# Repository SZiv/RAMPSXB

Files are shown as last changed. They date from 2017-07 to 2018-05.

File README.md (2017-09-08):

# RAMPSXB
For anyone who does extensive, hardcore, overkill 3D printer work, will typically run out of either stepper motor slots for extruders, MOSFETS for Heaters/fans, or Thermistor pins. The options for this are to either upgrade to an expensive mainboard like a duet, or add on individial drivers for stepper or FET. There isn't really a cheap or easy option. 

Now there is! RAMPSXB is an expansion board for the popular control board RAMPS 1.4 that connects to the AUX and endstop headers like an arduino shield to add functionality to the system. in addition, most components and schematic layouts follow the Reprap Defacto standard, as well as the original RAMPS board, so the thermistors, FETs, microstepping and drivers should all behave as if they were an extension of the RAMPS board itself. Most components are dirt cheap, and the board can be outsourced and assembled with a simple soldering iron. 

RAMPSXB is an expansion board shield for serious 3D printer people that adds an overkill amount of functionality to run high-end extruder systems like the E3D Kraken or Diamond Full Color Hotend: 

- 4 additional Stepper motors (bringing the total to 9; enough to run 6 extruders) 
- 4 additional Thermistor pins
- 4 additional MOSFETs w/ PWM control
- EXP1 and EXP2 headers for a Reprap Full Graphics Smart Controller (With SD Card)
- 4 additional 12V rail pins w/ grounds
- 4 additional 5V rail pins w/ grounds
- 2 steppers have two rows of output pins for driving 2 motors together
- Broken out, preregulated pins for HC-05 Bluetooth Chip
- Isolated input and microcontroller power, so 12V or 24V power can be used for the FETs. 
- Suppression Capacitors on endstops to reduce false positives caused by inductive voltages.
- 1 servo pin (the other 3 were consumed for PWM on the FETs, but are broken out if you want to use them for something other than the FETS)
- Broken out 12C pins 

This comes at the cost of: 
- 3 of the 4 servo pins. 
- Max endstops (there are only min endstops)
- AAAAAAALL the AUX headers (with the exception of 1 digital pin, D40, which is broken out)
- A lot of additional space

If you have questions, feel free to shoot me a message, or if you want to learn more about the making of this project, see here: http://scottziv.com/rampsxb

Be sure to take a look at the Wiki here: http://reprap.org/wiki/RAMPSXB

Happy printing!

Released under GPL V3

# Pin Definitions

E2 Direction      -  15  
E2 Step           -  19  
E2 Enable         -  63  
E3 Direction      -  2  
E3 Step           -  39  
E3 Enable         -  58  
E4 Direction      -  42  
E4 Step           -  44  
E4 Enable         -  43  
E5 Direction      -  32  
E5 Step           -  47  
E5 Enable         -  57  
Thermistor T3     -  A11  
Thermistor T4     -  A12  
Thermistor T5     -  A10  
Thermistor T6     -  A5  
MOSFET H3          -  4  
MOSFET H4          -  5  
MOSFET H5          -  6  
MOSFET H6          -  45    

HC-05 chip, LCD screen, and SD card follow the standard pinouts for the Full Graphic smart controller and RAMPS HC-05 attachment.

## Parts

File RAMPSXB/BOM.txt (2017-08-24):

---- Bill of Materials ----  

Part                                      Quantity          Package  

Electrolytic Capacitors, 100uF, SMD         4                 0605  
Electrolytic Capacitors, 10uF, SMD          4                 0405  
Nonpolarized Capacitor, SMD, 0.47uF         3                 0805  
Resistors, SMD, 100k Ohm                    8                 0805  
Resistors, SMD, 10k Ohm                     4                 0805  
Resistors, SMD, 10 Ohm                      4                 0805  
Resistors, SMD, 1.8k Ohm                    4                 0805  
Resistors, SMD, 4.7k Ohm                    4                 0805  
Resistors, SMD, 3.3k Ohm                    1                 0805  
Resistors, SMD, 2.2k Ohm                    1                 0805  
MOSFET, Through-hole, stp55nf06l            4                 TO-220  
LEDs, SMD                                   4                 0805  
Screw Terminals                             5                 3.5mm  
PTC Fuse, 30V 6A-9A                         1                
Pin Headers, 1x18, female, 0.1" spacing     1                 N/A   
Pin Headers, 1x8, female, 0.1" spacing      8                 N/A  
Pin Headers, 2x10, female, 0.1" spacing     1                 N/A  
Pin Headers, 2x4, female, 0.1" spacing      3                 N/A
Pin Headers, 1x4, female, 0.1" spacing      2                 N/A
Pin Headers, 1x6, female, 0.1" spacing      3                 N/A  
Pin Headers, 1x1, male, 0.1" spacing        1                 N/A  
Pin Headers, 2x4, male, 0.1" spacing        6                 N/A  
Pin Headers, 1x4, male, 0.1" spacing        3                 N/A  
Pin Headers, 2x5, male, 0.1" spacing        2                 N/A
Pin Headers, 2x2, male, 0.1" spacing        1                 N/A  
Pin Headers, 1x3, male, 0.1" spacing        4                 N/A

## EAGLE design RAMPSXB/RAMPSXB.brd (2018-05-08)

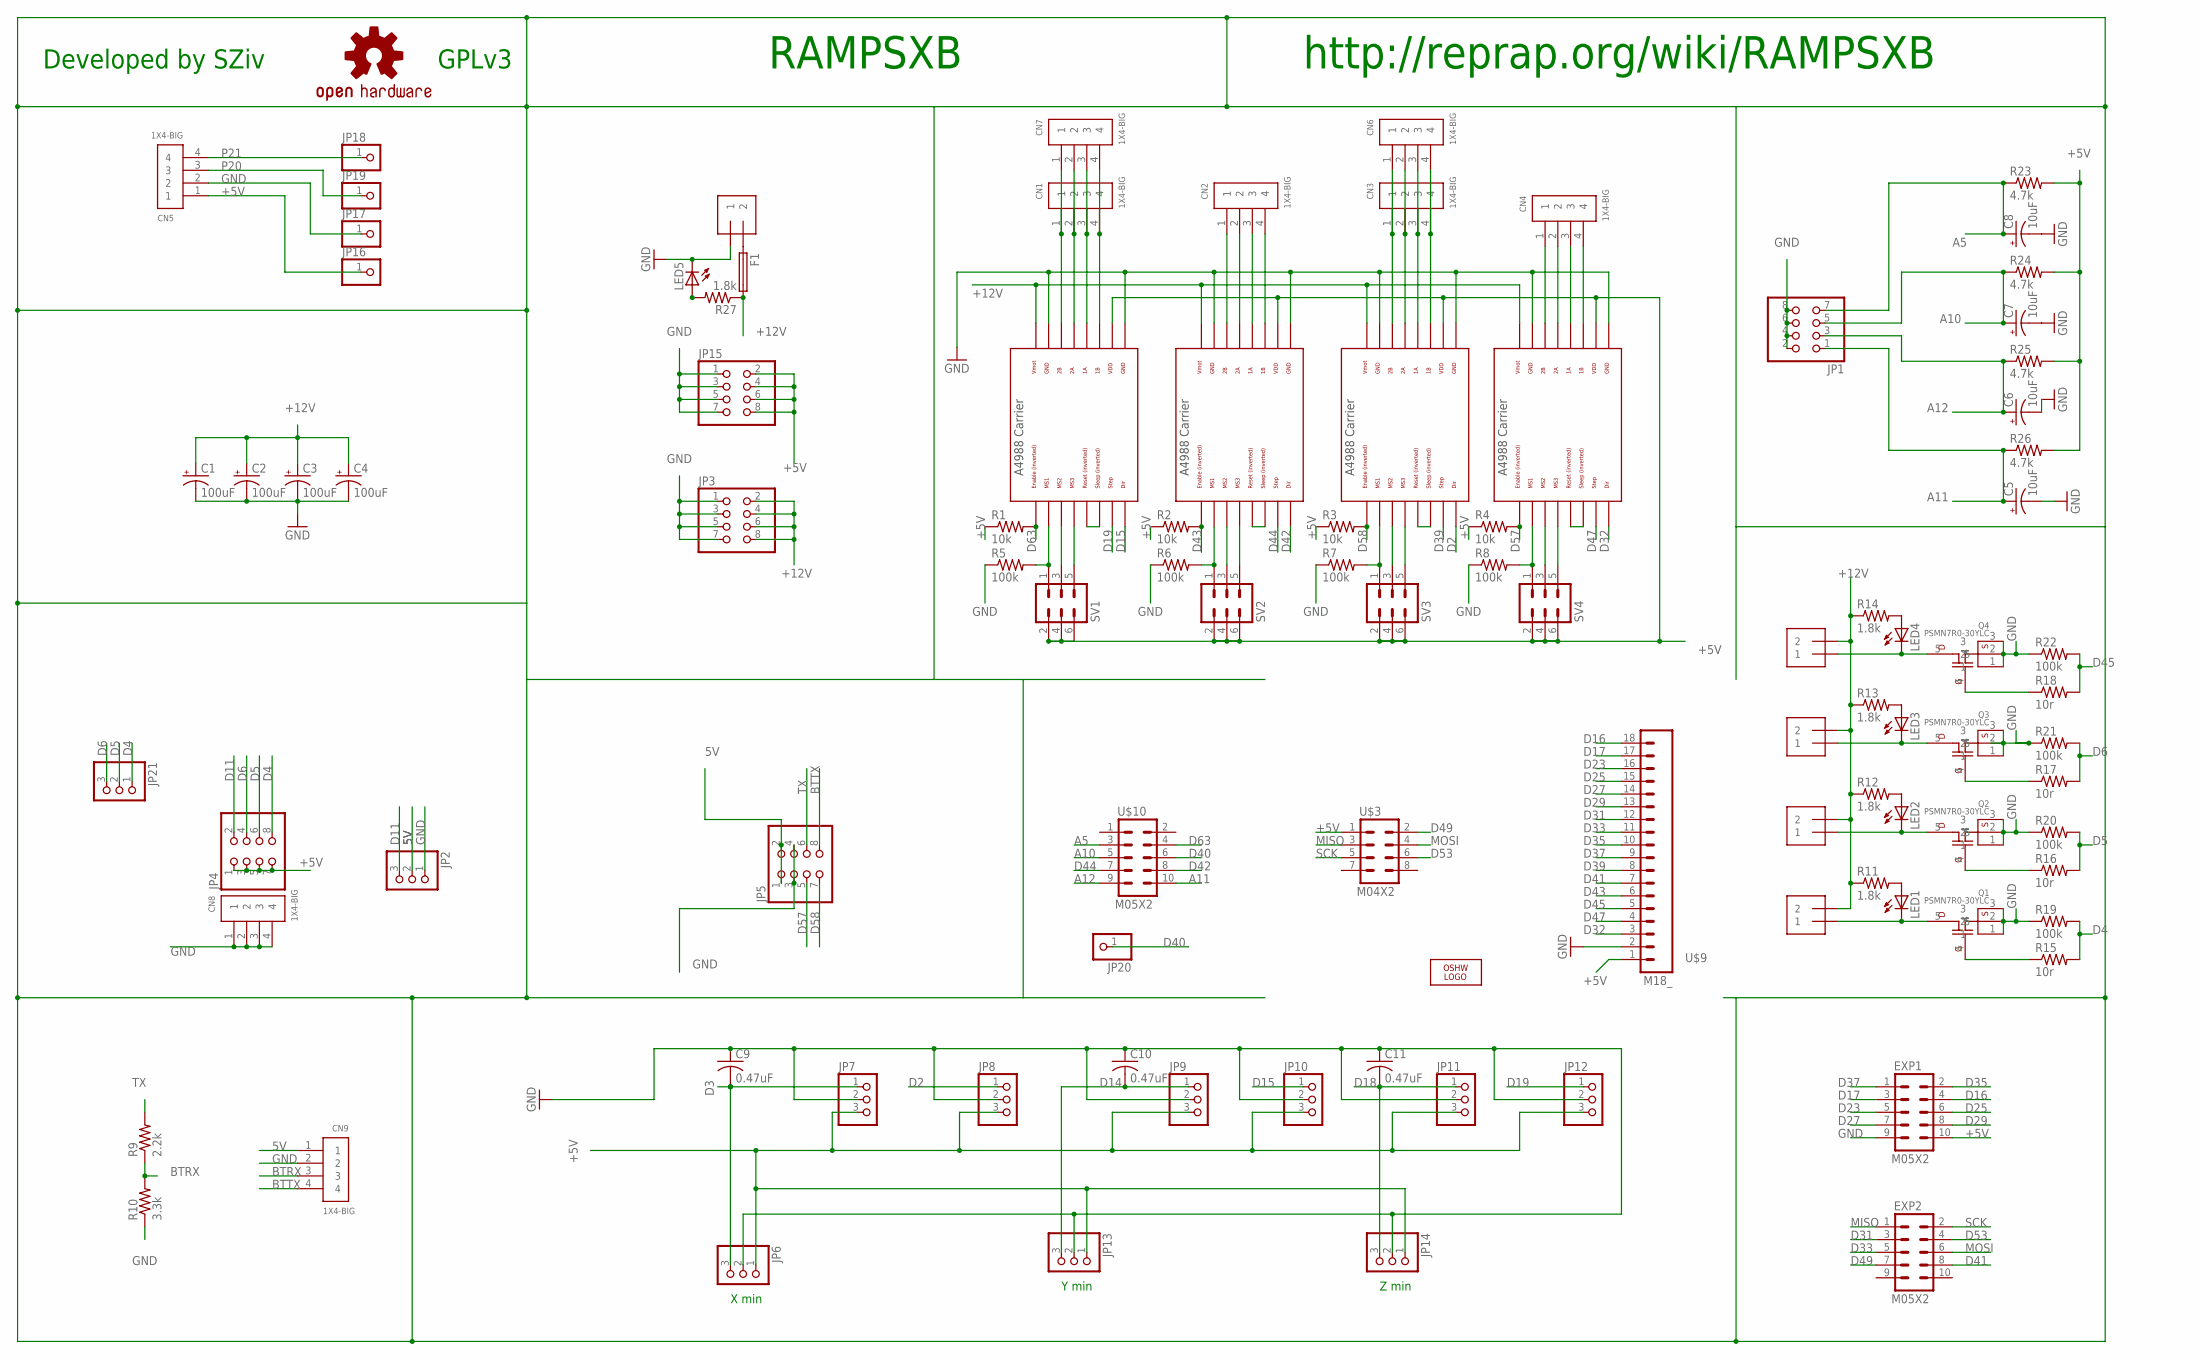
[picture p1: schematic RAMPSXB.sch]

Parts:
C1, C2, C3, C4: 100uF; 153CLV-0605
C5, C6, C7, C8: 10uF; 153CLV-0405
C9, C10, C11: 0.47uF; C0805
CN1, CN2, CN3, CN4, CN5, CN6, CN7, CN8, CN9: 1X4-BIG; 1X04-BIG
EXP1, EXP2: M05X2; 2X5
F1: PTCFUSE; LITTLEFUSE
J1, J2, J3, J4, J5: 1X2-3.5MM
JP1, JP3, JP4, JP5, JP15: PINHD-2X4; 2X04
JP2, JP6, JP7, JP8, JP9, JP10, JP11, JP12, JP13, JP14, JP21: PINHD-1X3; 1X03
JP16, JP17, JP18, JP19, JP20: PINHD-1X1; 1X01
LED1, LED2, LED3, LED4, LED5: LEDCHIPLED_0805; CHIPLED_0805
LOGO1: OSHW_LOGO_6MILX0100-NT; OSHW_6X100_NOTEXT
LOGO2: OSHW-LOGOL; OSHW-LOGO-L
Q1, Q2, Q3, Q4: PSMN7R0-30YLC; LFPAK
R1, R2, R3, R4: 10k; M0805
R5, R6, R7, R8, R19, R20, R21, R22: 100k; M0805
R9: 2.2k; M0805
R10: 3.3k; M0805
R11, R12, R13, R14, R27: 1.8k; M0805
R15, R16, R17, R18: 10r; M0805
R23, R24, R25, R26: 4.7k; R0805
SV1, SV2, SV3, SV4: MA03-2
U$1, U$2, U$4, U$5: POLOLU_A4983CARRIER; A4988BREAKOUT
U$3: M04X2; 2X4
U$9: M18_; 1X18
U$10: M05X2; 2X5

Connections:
5V: CN9.1, JP2.2, JP5.1, JP5.2
+5V: CN5.1, EXP1.10, JP4.1, JP4.3, JP4.5, JP4.7, JP6.1, JP7.3, JP8.3, JP9.3, JP10.3, JP11.3, JP12.3, JP13.1, JP14.1, JP15.2, JP15.4, JP15.6, JP15.8, JP16.1, R1.1, R2.1, R3.1, R4.1, R23.2, R24.2, R25.2, R26.2, SV1.2, SV1.4, SV1.6, SV2.2, SV2.4, SV2.6, SV3.2, SV3.4, SV3.6, SV4.2, SV4.4, SV4.6, U$1.VDD, U$2.VDD, U$3.1, U$4.VDD, U$5.VDD, U$9.1
+12V: C1.+, C2.+, C3.+, C4.+, F1.2, J2.2, J3.2, J4.2, J5.2, JP3.2, JP3.4, JP3.6, JP3.8, R11.1, R12.1, R13.1, R14.1, R27.1, U$1.VMOT, U$2.VMOT, U$4.VMOT, U$5.VMOT
A5: C8.+, JP1.7, R23.1, U$10.3
A10: C7.+, JP1.5, R24.1, U$10.5
A11: C5.+, JP1.1, R26.1, U$10.10
A12: C6.+, JP1.3, R25.1, U$10.9
BTRX: CN9.3, R9.1, R10.2
BTTX: CN9.4, JP5.8
D2: JP8.1, U$4.DIR
D3: C9.2, JP6.3, JP7.1
D4: JP4.8, JP21.1, R15.2, R19.2
D5: JP4.6, JP21.2, R16.2, R20.2
D6: JP4.4, JP21.3, R17.2, R21.2
D11: JP2.3, JP4.2
D14: C10.2, JP9.1, JP13.3
D15: JP10.1, U$1.DIR
D16: EXP1.4, U$9.18
D17: EXP1.3, U$9.17
D18: C11.2, JP11.1, JP14.3
D19: JP12.1, U$1.STEP
D23: EXP1.5, U$9.16
D25: EXP1.6, U$9.15
D27: EXP1.7, U$9.14
D29: EXP1.8, U$9.13
D31: EXP2.3, U$9.12
D32: U$5.DIR, U$9.3
D33: EXP2.5, U$9.11
D35: EXP1.2, U$9.10
D37: EXP1.1, U$9.9
D39: U$4.STEP, U$9.8
D40: JP20.1, U$10.6
D41: EXP2.8, U$9.7
D42: U$2.DIR, U$10.8
D43: R2.2, U$2.EN, U$9.6
D44: U$2.STEP, U$10.7
D45: R18.2, R22.2, U$9.5
D47: U$5.STEP, U$9.4
D49: EXP2.7, U$3.2
D53: EXP2.4, U$3.6
D57: JP5.5, R4.2, U$5.EN
D58: JP5.7, R3.2, U$4.EN
D63: R1.2, U$1.EN, U$10.4
GND: C1.-, C2.-, C3.-, C4.-, C5.-, C6.-, C7.-, C8.-, C9.1, C10.1, C11.1, CN5.2, CN8.1, CN8.2, CN8.3, CN8.4, CN9.2, EXP1.9, J1.1, JP1.2, JP1.4, JP1.6, JP1.8, JP2.1, JP3.1, JP3.3, JP3.5, JP3.7, JP5.3, JP5.4, JP6.2, JP7.2, JP8.2, JP9.2, JP10.2, JP11.2, JP12.2, JP13.2, JP14.2, JP15.1, JP15.3, JP15.5, JP15.7, JP17.1, LED5.C, Q1.1, Q1.2, Q1.3, Q2.1, Q2.2, Q2.3, Q3.1, Q3.2, Q3.3, Q4.1, Q4.2, Q4.3, R5.1, R6.1, R7.1, R8.1, R10.1, R19.1, R20.1, R21.1, R22.1, U$1.GND, U$1.GND@0 (GND), U$2.GND, U$2.GND@0 (GND), U$4.GND, U$4.GND@0 (GND), U$5.GND, U$5.GND@0 (GND), U$9.2
MISO: EXP2.1, U$3.3
MOSI: EXP2.6, U$3.4
unnamed: CN1.1, CN7.1, U$1.2B
unnamed: LED5.A, R27.2
unnamed: CN1.3, CN7.3, U$1.1A
unnamed: CN1.4, CN7.4, U$1.1B
unnamed: CN2.1, U$2.2B
unnamed: CN2.2, U$2.2A
unnamed: CN2.3, U$2.1A
unnamed: CN2.4, U$2.1B
unnamed: CN3.1, CN6.1, U$4.2B
unnamed: CN3.2, CN6.2, U$4.2A
unnamed: CN3.3, CN6.3, U$4.1A
unnamed: CN3.4, CN6.4, U$4.1B
unnamed: CN4.1, U$5.2B
unnamed: CN4.2, U$5.2A
unnamed: CN4.3, U$5.1A
unnamed: CN4.4, U$5.1B
unnamed: F1.1, J1.2
unnamed: R5.2, SV1.1, U$1.MS1
unnamed: SV1.3, U$1.MS2
unnamed: SV1.5, U$1.MS3
unnamed: R6.2, SV2.1, U$2.MS1
unnamed: SV2.3, U$2.MS2
unnamed: SV2.5, U$2.MS3
unnamed: R7.2, SV3.1, U$4.MS1
unnamed: SV3.3, U$4.MS2
unnamed: SV3.5, U$4.MS3
unnamed: R8.2, SV4.1, U$5.MS1
unnamed: SV4.3, U$5.MS2
unnamed: SV4.5, U$5.MS3
unnamed: J2.1, LED1.C, Q1.5
unnamed: U$2.RST, U$2.SLP (SLEEP)
unnamed: U$1.RST, U$1.SLP (SLEEP)
unnamed: U$4.RST, U$4.SLP (SLEEP)
unnamed: U$5.RST, U$5.SLP (SLEEP)
unnamed: J3.1, LED2.C, Q2.5
unnamed: J4.1, LED3.C, Q3.5
unnamed: J5.1, LED4.C, Q4.5
unnamed: LED1.A, R11.2
unnamed: LED2.A, R12.2
unnamed: LED3.A, R13.2
unnamed: LED4.A, R14.2
unnamed: CN1.2, CN7.2, U$1.2A
unnamed: Q3.4, R17.1
unnamed: Q4.4, R18.1
unnamed: Q2.4, R16.1
unnamed: Q1.4, R15.1
P20: CN5.3, JP19.1
P21: CN5.4, JP18.1
SCK: EXP2.2, U$3.5
TX: JP5.6, R9.2

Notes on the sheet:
X min
Y min
Z min
RAMPSXB
http://reprap.org/wiki/RAMPSXB
Developed by SZiv
GPLv3

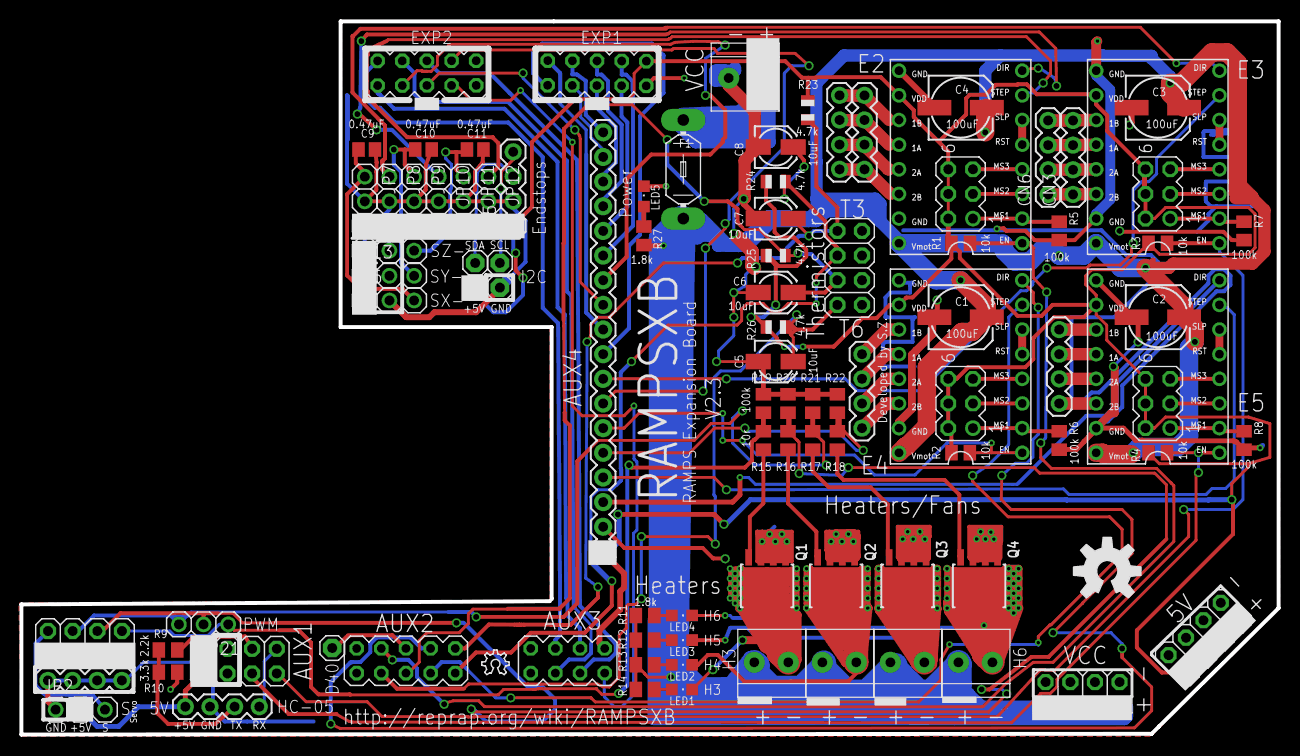
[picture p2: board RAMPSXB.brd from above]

Board: 2 copper layers, 129.5 x 73.5 mm, 98 parts (0 on the bottom side), 96 nets.

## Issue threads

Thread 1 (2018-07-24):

Feature Request: Closed loop stepper control

npgoalkeeper, 2018-07-24:
I was just curious if closed-loop stepper control was possible, among other things, such as tmc 2130/2100/2208/2660 control (along with an ADC converter to adjust voltage). Possibly even an SD card or ethernet slot to load stl files. Heck, maybe even a tl-smoother configuration.

Closed 2018-11-23.

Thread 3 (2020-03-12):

Bill of Materials incomplete

kaliber64, 2020-03-12:
Capacitors need voltage ratings
Resisters need wattage dissipation ratings
As well as the specifics on the MOSFET so a suitable one can be found.
A complete Bill of Materials needs Manufacture Part Numbers however suitable ones can usually be found by the manufacturer during the Quote process.

alexws54tk, 2021-02-26:
1. If you prefer powered 12V -- Capacitors min voltage rating is 16V. If you prefer powered 24V or higher -- Capacitors min voltage rating is 50V
2. 1/4W resistor.

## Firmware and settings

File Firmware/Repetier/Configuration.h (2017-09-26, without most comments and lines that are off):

#define CONFIGURATION_H
#define NUM_EXTRUDER 6
#define MOTHERBOARD 33
#include "pins.h"
#undef FAN_BOARD_PIN
#define FAN_BOARD_PIN -1
#define BOARD_FAN_SPEED 255
#define FAN_THERMO_PIN -1
#define FAN_THERMO_MIN_PWM 128
#define FAN_THERMO_MAX_PWM 255
#define FAN_THERMO_MIN_TEMP 45
#define FAN_THERMO_MAX_TEMP 60
#define FAN_THERMO_THERMISTOR_PIN -1
#define FAN_THERMO_THERMISTOR_TYPE 1
#undef X_MAX_PIN
#define X_MAX_PIN -1
#undef Y_MAX_PIN
#define Y_MAX_PIN -1
#undef Z_MAX_PIN
#define Z_MAX_PIN -1
#define BLUETOOTH_SERIAL  -1
#define BLUETOOTH_BAUD  115200
#define MIXING_EXTRUDER 0
#define DRIVE_SYSTEM 0
#define XAXIS_STEPS_PER_MM 80
#define YAXIS_STEPS_PER_MM 80
#define ZAXIS_STEPS_PER_MM 80
#define EXTRUDER_FAN_COOL_TEMP 50
#define PDM_FOR_EXTRUDER 0
#define PDM_FOR_COOLER 0
#define DECOUPLING_TEST_MAX_HOLD_VARIANCE 20
#define DECOUPLING_TEST_MIN_TEMP_RISE 1
#define KILL_IF_SENSOR_DEFECT 0
#define RETRACT_ON_PAUSE 2
#define PAUSE_START_COMMANDS ""
#define PAUSE_END_COMMANDS ""
#define SHARED_EXTRUDER_HEATER 0
#define EXT0_X_OFFSET 0
#define EXT0_Y_OFFSET 0
#define EXT0_Z_OFFSET 0
#define EXT0_STEPS_PER_MM 370
#define EXT0_TEMPSENSOR_TYPE 1
#define EXT0_TEMPSENSOR_PIN TEMP_0_PIN
#define EXT0_HEATER_PIN HEATER_0_PIN
#define EXT0_STEP_PIN ORIG_E0_STEP_PIN
#define EXT0_DIR_PIN ORIG_E0_DIR_PIN
#define EXT0_INVERSE 0
#define EXT0_ENABLE_PIN ORIG_E0_ENABLE_PIN
#define EXT0_ENABLE_ON 0
#define EXT0_MIRROR_STEPPER 0
#define EXT0_STEP2_PIN ORIG_E0_STEP_PIN
#define EXT0_DIR2_PIN ORIG_E0_DIR_PIN
#define EXT0_INVERSE2 0
#define EXT0_ENABLE2_PIN ORIG_E0_ENABLE_PIN
#define EXT0_MAX_FEEDRATE 50
#define EXT0_MAX_START_FEEDRATE 20
#define EXT0_MAX_ACCELERATION 5000
#define EXT0_HEAT_MANAGER 3
#define EXT0_WATCHPERIOD 1
#define EXT0_PID_INTEGRAL_DRIVE_MAX 230
#define EXT0_PID_INTEGRAL_DRIVE_MIN 40
#define EXT0_PID_PGAIN_OR_DEAD_TIME 7
#define EXT0_PID_I 2
#define EXT0_PID_D 40
#define EXT0_PID_MAX 255
#define EXT0_ADVANCE_K 0
#define EXT0_ADVANCE_L 0
#define EXT0_ADVANCE_BACKLASH_STEPS 0
#define EXT0_WAIT_RETRACT_TEMP 150
#define EXT0_WAIT_RETRACT_UNITS 0
#define EXT0_SELECT_COMMANDS ""
#define EXT0_DESELECT_COMMANDS ""
#define EXT0_EXTRUDER_COOLER_PIN -1
#define EXT0_EXTRUDER_COOLER_SPEED 255
#define EXT0_DECOUPLE_TEST_PERIOD 12000
#define EXT0_JAM_PIN -1
#define EXT0_JAM_PULLUP 0
#define EXT1_X_OFFSET 0
#define EXT1_Y_OFFSET 0
#define EXT1_Z_OFFSET 0
#define EXT1_STEPS_PER_MM 370
#define EXT1_TEMPSENSOR_TYPE 1
#define EXT1_TEMPSENSOR_PIN TEMP_2_PIN
#define EXT1_HEATER_PIN HEATER_2_PIN
#define EXT1_STEP_PIN ORIG_E1_STEP_PIN
#define EXT1_DIR_PIN ORIG_E1_DIR_PIN
#define EXT1_INVERSE 0
#define EXT1_ENABLE_PIN ORIG_E1_ENABLE_PIN
#define EXT1_ENABLE_ON 0
#define EXT1_MIRROR_STEPPER 0
#define EXT1_STEP2_PIN ORIG_E1_STEP_PIN
#define EXT1_DIR2_PIN ORIG_E1_DIR_PIN
#define EXT1_INVERSE2 0
#define EXT1_ENABLE2_PIN ORIG_E1_ENABLE_PIN
#define EXT1_MAX_FEEDRATE 50
#define EXT1_MAX_START_FEEDRATE 20
#define EXT1_MAX_ACCELERATION 5000
#define EXT1_HEAT_MANAGER 3
#define EXT1_WATCHPERIOD 1
#define EXT1_PID_INTEGRAL_DRIVE_MAX 230
#define EXT1_PID_INTEGRAL_DRIVE_MIN 40
#define EXT1_PID_PGAIN_OR_DEAD_TIME 7
#define EXT1_PID_I 2
#define EXT1_PID_D 40
#define EXT1_PID_MAX 255
#define EXT1_ADVANCE_K 0
#define EXT1_ADVANCE_L 0
#define EXT1_ADVANCE_BACKLASH_STEPS 0
#define EXT1_WAIT_RETRACT_TEMP 150
#define EXT1_WAIT_RETRACT_UNITS 0
#define EXT1_SELECT_COMMANDS ""
#define EXT1_DESELECT_COMMANDS ""
#define EXT1_EXTRUDER_COOLER_PIN -1
#define EXT1_EXTRUDER_COOLER_SPEED 255
#define EXT1_DECOUPLE_TEST_PERIOD 12000
#define EXT1_JAM_PIN -1
#define EXT1_JAM_PULLUP 0
#define EXT2_X_OFFSET 0
#define EXT2_Y_OFFSET 0
#define EXT2_Z_OFFSET 0
#define EXT2_STEPS_PER_MM 370
#define EXT2_TEMPSENSOR_TYPE 1
#define EXT2_TEMPSENSOR_PIN 11
#define EXT2_HEATER_PIN 4
#define EXT2_STEP_PIN ORIG_E2_STEP_PIN
#define EXT2_DIR_PIN ORIG_E2_DIR_PIN
#define EXT2_INVERSE 0
#define EXT2_ENABLE_PIN ORIG_E2_ENABLE_PIN
#define EXT2_ENABLE_ON 0
#define EXT2_MIRROR_STEPPER 0
#define EXT2_STEP2_PIN ORIG_E2_STEP_PIN
#define EXT2_DIR2_PIN ORIG_E2_DIR_PIN
#define EXT2_INVERSE2 0
#define EXT2_ENABLE2_PIN ORIG_E2_ENABLE_PIN
#define EXT2_MAX_FEEDRATE 50
#define EXT2_MAX_START_FEEDRATE 20
#define EXT2_MAX_ACCELERATION 5000
#define EXT2_HEAT_MANAGER 3
#define EXT2_WATCHPERIOD 1
#define EXT2_PID_INTEGRAL_DRIVE_MAX 230
#define EXT2_PID_INTEGRAL_DRIVE_MIN 40
#define EXT2_PID_PGAIN_OR_DEAD_TIME 7
#define EXT2_PID_I 2
#define EXT2_PID_D 40
#define EXT2_PID_MAX 255
#define EXT2_ADVANCE_K 0
#define EXT2_ADVANCE_L 0
#define EXT2_ADVANCE_BACKLASH_STEPS 0
#define EXT2_WAIT_RETRACT_TEMP 150
#define EXT2_WAIT_RETRACT_UNITS 0
#define EXT2_SELECT_COMMANDS ""
#define EXT2_DESELECT_COMMANDS ""
#define EXT2_EXTRUDER_COOLER_PIN -1
#define EXT2_EXTRUDER_COOLER_SPEED 255
#define EXT2_DECOUPLE_TEST_PERIOD 12000
#define EXT2_JAM_PIN -1
#define EXT2_JAM_PULLUP 0
#define EXT3_X_OFFSET 0
#define EXT3_Y_OFFSET 0
#define EXT3_Z_OFFSET 0
#define EXT3_STEPS_PER_MM 370
#define EXT3_TEMPSENSOR_TYPE 1
#define EXT3_TEMPSENSOR_PIN 12
#define EXT3_HEATER_PIN 5
#define EXT3_STEP_PIN ORIG_E3_STEP_PIN
#define EXT3_DIR_PIN ORIG_E3_DIR_PIN
#define EXT3_INVERSE 0
#define EXT3_ENABLE_PIN ORIG_E3_ENABLE_PIN
#define EXT3_ENABLE_ON 0
#define EXT3_MIRROR_STEPPER 0
#define EXT3_STEP2_PIN ORIG_E3_STEP_PIN
#define EXT3_DIR2_PIN ORIG_E3_DIR_PIN
#define EXT3_INVERSE2 0
#define EXT3_ENABLE2_PIN ORIG_E3_ENABLE_PIN
#define EXT3_MAX_FEEDRATE 50
#define EXT3_MAX_START_FEEDRATE 20
#define EXT3_MAX_ACCELERATION 5000
#define EXT3_HEAT_MANAGER 3
#define EXT3_WATCHPERIOD 1
#define EXT3_PID_INTEGRAL_DRIVE_MAX 230
#define EXT3_PID_INTEGRAL_DRIVE_MIN 40
#define EXT3_PID_PGAIN_OR_DEAD_TIME 7
#define EXT3_PID_I 2
#define EXT3_PID_D 40
#define EXT3_PID_MAX 255
#define EXT3_ADVANCE_K 0
#define EXT3_ADVANCE_L 0
#define EXT3_ADVANCE_BACKLASH_STEPS 0
#define EXT3_WAIT_RETRACT_TEMP 150
#define EXT3_WAIT_RETRACT_UNITS 0
#define EXT3_SELECT_COMMANDS ""
#define EXT3_DESELECT_COMMANDS ""
#define EXT3_EXTRUDER_COOLER_PIN -1
#define EXT3_EXTRUDER_COOLER_SPEED 255
#define EXT3_DECOUPLE_TEST_PERIOD 12000
#define EXT3_JAM_PIN -1
#define EXT3_JAM_PULLUP 0
#define EXT4_X_OFFSET 0
#define EXT4_Y_OFFSET 0
#define EXT4_Z_OFFSET 0
#define EXT4_STEPS_PER_MM 370
#define EXT4_TEMPSENSOR_TYPE 1
#define EXT4_TEMPSENSOR_PIN 10
#define EXT4_HEATER_PIN 6
#define EXT4_STEP_PIN ORIG_E4_STEP_PIN
#define EXT4_DIR_PIN ORIG_E4_DIR_PIN
#define EXT4_INVERSE 0
#define EXT4_ENABLE_PIN ORIG_E4_ENABLE_PIN
#define EXT4_ENABLE_ON 0
#define EXT4_MIRROR_STEPPER 0
#define EXT4_STEP2_PIN ORIG_E4_STEP_PIN
#define EXT4_DIR2_PIN ORIG_E4_DIR_PIN
#define EXT4_INVERSE2 0
#define EXT4_ENABLE2_PIN ORIG_E4_ENABLE_PIN
#define EXT4_MAX_FEEDRATE 50
#define EXT4_MAX_START_FEEDRATE 20
#define EXT4_MAX_ACCELERATION 5000
#define EXT4_HEAT_MANAGER 3
#define EXT4_WATCHPERIOD 1
#define EXT4_PID_INTEGRAL_DRIVE_MAX 230
#define EXT4_PID_INTEGRAL_DRIVE_MIN 40
#define EXT4_PID_PGAIN_OR_DEAD_TIME 7
#define EXT4_PID_I 2
#define EXT4_PID_D 40
#define EXT4_PID_MAX 255
#define EXT4_ADVANCE_K 0
#define EXT4_ADVANCE_L 0
#define EXT4_ADVANCE_BACKLASH_STEPS 0
#define EXT4_WAIT_RETRACT_TEMP 150
#define EXT4_WAIT_RETRACT_UNITS 0
#define EXT4_SELECT_COMMANDS ""
#define EXT4_DESELECT_COMMANDS ""
#define EXT4_EXTRUDER_COOLER_PIN -1
#define EXT4_EXTRUDER_COOLER_SPEED 255
#define EXT4_DECOUPLE_TEST_PERIOD 12000
#define EXT4_JAM_PIN -1
#define EXT4_JAM_PULLUP 0
#define EXT5_X_OFFSET 0
#define EXT5_Y_OFFSET 0
#define EXT5_Z_OFFSET 0
#define EXT5_STEPS_PER_MM 370
#define EXT5_TEMPSENSOR_TYPE 1
#define EXT5_TEMPSENSOR_PIN 5
#define EXT5_HEATER_PIN 45
#define EXT5_STEP_PIN ORIG_E5_STEP_PIN
#define EXT5_DIR_PIN ORIG_E5_DIR_PIN
#define EXT5_INVERSE 0
#define EXT5_ENABLE_PIN ORIG_E5_ENABLE_PIN
#define EXT5_ENABLE_ON 0
#define EXT5_MIRROR_STEPPER 0
#define EXT5_STEP2_PIN ORIG_E5_STEP_PIN
#define EXT5_DIR2_PIN ORIG_E5_DIR_PIN
#define EXT5_INVERSE2 0
#define EXT5_ENABLE2_PIN ORIG_E5_ENABLE_PIN
#define EXT5_MAX_FEEDRATE 50
#define EXT5_MAX_START_FEEDRATE 20
#define EXT5_MAX_ACCELERATION 5000
#define EXT5_HEAT_MANAGER 3
#define EXT5_WATCHPERIOD 1
#define EXT5_PID_INTEGRAL_DRIVE_MAX 230
#define EXT5_PID_INTEGRAL_DRIVE_MIN 40
#define EXT5_PID_PGAIN_OR_DEAD_TIME 7
#define EXT5_PID_I 2
#define EXT5_PID_D 40
#define EXT5_PID_MAX 255
#define EXT5_ADVANCE_K 0
#define EXT5_ADVANCE_L 0
#define EXT5_ADVANCE_BACKLASH_STEPS 0
#define EXT5_WAIT_RETRACT_TEMP 150
#define EXT5_WAIT_RETRACT_UNITS 0
#define EXT5_SELECT_COMMANDS ""
#define EXT5_DESELECT_COMMANDS ""
#define EXT5_EXTRUDER_COOLER_PIN -1
#define EXT5_EXTRUDER_COOLER_SPEED 255
#define EXT5_DECOUPLE_TEST_PERIOD 12000
#define EXT5_JAM_PIN -1
#define EXT5_JAM_PULLUP 0
#define FEATURE_RETRACTION 1
#define AUTORETRACT_ENABLED 0
#define RETRACTION_LENGTH 3
#define RETRACTION_LONG_LENGTH 13
#define RETRACTION_SPEED 40
#define RETRACTION_Z_LIFT 0
#define RETRACTION_UNDO_EXTRA_LENGTH 0
#define RETRACTION_UNDO_EXTRA_LONG_LENGTH 0
#define RETRACTION_UNDO_SPEED 20
#define FILAMENTCHANGE_X_POS 0
#define FILAMENTCHANGE_Y_POS 0
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

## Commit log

2017-07-25 Main Commit
    First Commit
    [RAMPSXB.brd, RAMPSXB.sch]
2017-07-27 V2!
    V2 release. Full PWM, Bluetooth, Larger board.
    [RAMPSXB.brd, RAMPSXB.sch]
2017-07-27 Seperated out BOM
2017-08-05 Removed Old RAMPS version.
    SD card slot did not have logic level shifter, so it would fry SD cards
    inserted into it. Whoops.
    Removed all files so people wouldnt accidently make it
    [RAMPSXB.brd, RAMPSXB.sch]
2017-08-08 Rerouting, broken out PWM pins
    Rerouting, broken out PWM pins
    [RAMPSXB.brd, RAMPSXB.sch]
2017-08-23 Reroute
    Reroute of some wires
2017-08-23 Exposed Power Traces
    Exposed Traces to increase current by covering with solder
    [RAMPSXB.brd]
2017-08-24 Updated BOM. Dont know what happened.
2017-08-26 Added Power Indicator and fixed a short.
    Added Power indicator LED, and Fixed a major issue where +5V on the
    arduino was connected to ground. Whoops.
    [RAMPSXB.brd, RAMPSXB.sch]
2017-08-28 Added Gerber Files. Slight Rewiring.
    Added Gerber Files for production run. Fixed some clearance issues.
    [RAMPSXB.GBL, RAMPSXB.GBO, RAMPSXB.GBP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]
2017-08-28 Swapped pins 49 and 43. Documentation for the Smart Controller was incorrect.
    Almost everything works, but the SD card for some reason opens, but I
    cant read anything. Still working on that.
    [RAMPSXB.brd, RAMPSXB.sch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]
2017-08-28 Fixed the SD card issue. I wasn't wiring it right. ¯\_(ツ)_/¯
    No changes.
2017-08-29 Replaced FETs with PSMN7R0-30YLCs for production.
    Added Older Version Directory for the old STP55 board. It should also
    work as well.
    [RAMPSXB.GBL, RAMPSXB.GBO, RAMPSXB.GBP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]
2017-09-07 Expanded the traces on the FETs, corrected some incorrect pins on the infographic.
    [RAMPSXB.brd]
2017-09-25 Expanded Traces, Fixed Fonts
    Changed Fonts to Vector, so they come out in the right place. Expanded
    power traces.
    [RAMPSXB.brd, RAMPSXB.sch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]
2017-09-25 Fixed LED Numbering, updated V2.1
    LED Indicators were not on the right FETs. Not sure how I missed that.
    Updated V2.1 with corrected Vector Text.
    [RAMPSXB.GBL, RAMPSXB.GBO, RAMPSXB.GBP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]
2017-09-26 Fixed Incorrect label
    Incorrect Label on Pin listing. Had 2 D32s. Corrected to D42.
    [RAMPSXB.brd]
2017-09-26 Added Labeling for the Heater LEDs.
    So you know which one is which
    [RAMPSXB.brd]
2017-09-26 Updated Gerbers, Added the firmware
    Updated Gerbers and added a working firmware. The firmware is for a
    full-on 6 extruder mess using a Full Graphics Smart Controller. Unless
    you happen to have the same setup I do, You should go to the Repetier
    Firmware configurator and adapt it to your needs.
    [Configuration.h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]
2017-09-26 Incremented Version number and added a bigger OSHW Logo to fill in the empty space
    Hopefully, this should be close to the final version
    [RAMPSXB.brd, RAMPSXB.sch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]
2017-09-26 Fixed some issues with V2.1, and updated gerbers
    fixed some stuff with V2.1 and corrected some issues
    [RAMPSXB.brd, RAMPSXB.sch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]
2017-09-27 Labeling for R9 and R10 was flipped. Fixed.
    [Configuration.h, RAMPSXB.brd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]
2017-11-05 Minor Fixes
    Did some separation between the power leads because they are really
    close.
    Cleaned up the Silkscreen a little bit, and labeled servo pins.
    [RAMPSXB.brd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]
2018-05-08 flipped Min X and Min Z pin labeling
    Corrected an error where the labeling for the Min Z and Min X pins were
    flipped. Not sure how I missed that one!
    [RAMPSXB.brd]

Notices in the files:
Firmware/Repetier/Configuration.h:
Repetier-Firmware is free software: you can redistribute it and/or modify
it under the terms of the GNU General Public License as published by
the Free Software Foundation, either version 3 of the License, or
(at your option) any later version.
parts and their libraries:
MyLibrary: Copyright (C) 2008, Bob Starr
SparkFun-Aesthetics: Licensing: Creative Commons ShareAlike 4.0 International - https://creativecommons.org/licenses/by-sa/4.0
